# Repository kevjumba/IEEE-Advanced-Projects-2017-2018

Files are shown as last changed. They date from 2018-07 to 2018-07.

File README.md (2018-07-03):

# IEEE-Advanced-Projects-2017-2018

This is the collective work done by myself, Will Fehrnstrom, Ryan Nemiroff, and Amit Golan as part of the Advanced Projects project groups
at UCLA IEEE. 

The objective was the build a fully functioning quadcopter which entails designing the PCB using Eagle Cad and coding much of the
wireless connections and motor control using a MPU6050 and microprocessors(arduino).

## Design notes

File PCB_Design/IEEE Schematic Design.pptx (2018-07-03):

## IEEE Schematic Design

Will Fehrnstrom, Ryan Nemiroff, Kevin Zhang, Amit Golan

## RESET/FTDI

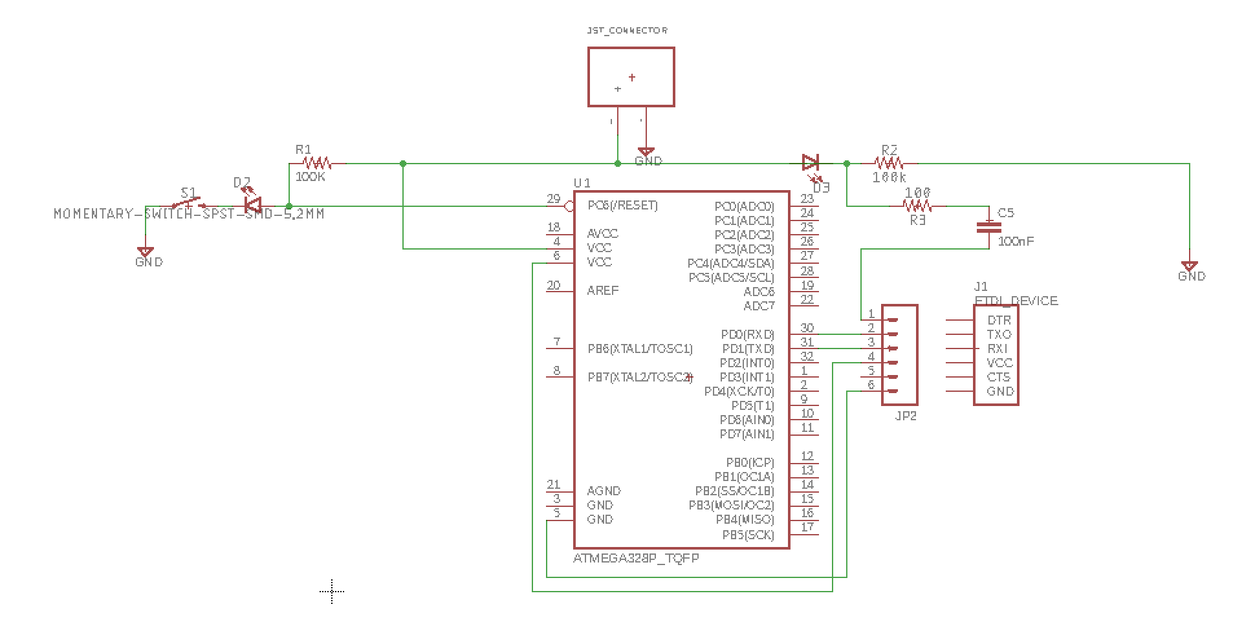
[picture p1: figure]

## Decoupling MCU

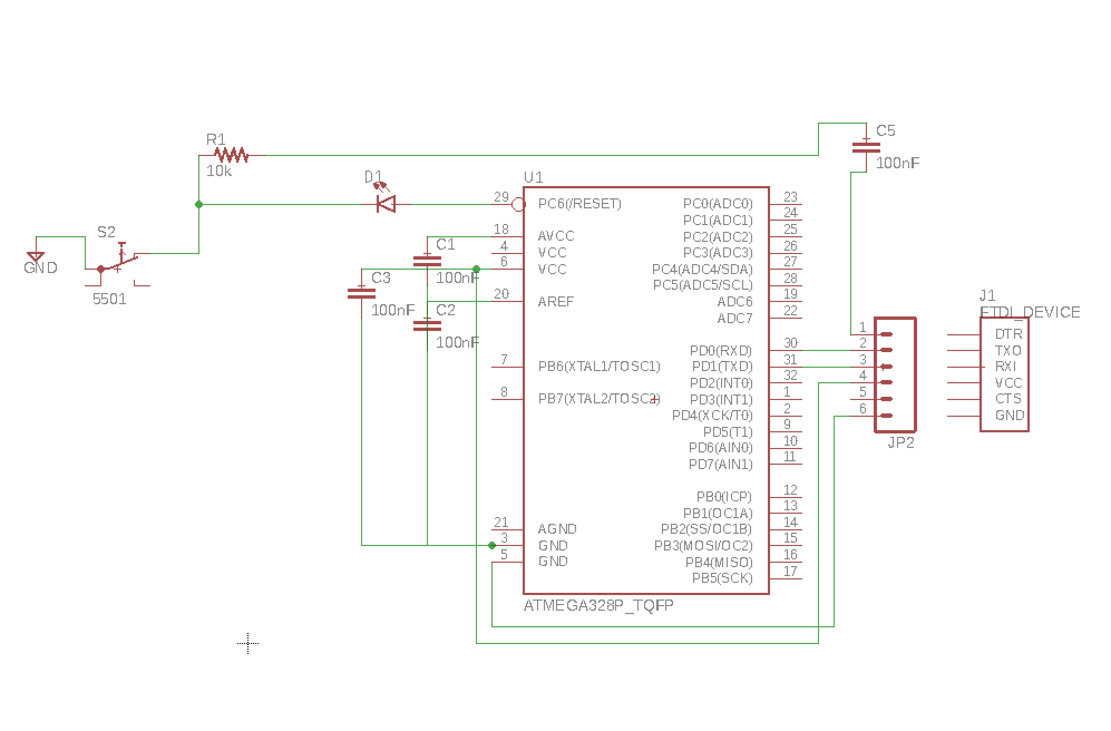
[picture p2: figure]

## Motor Driver

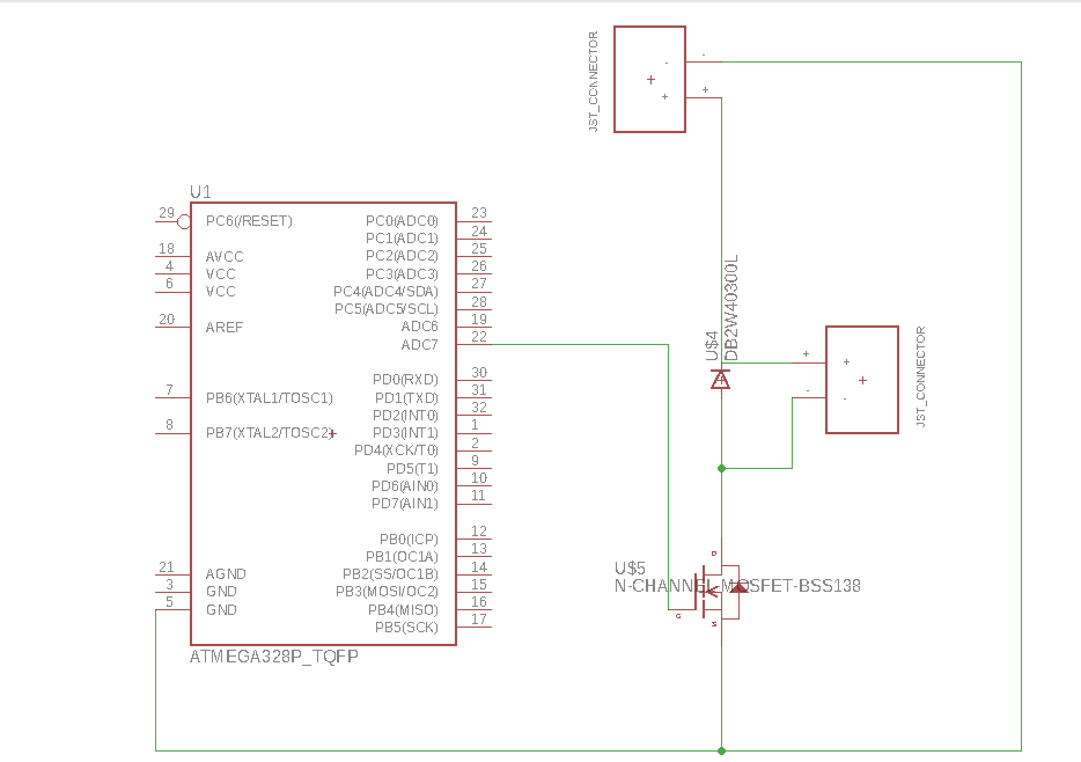
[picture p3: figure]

## IMU to MCU and voltage divider

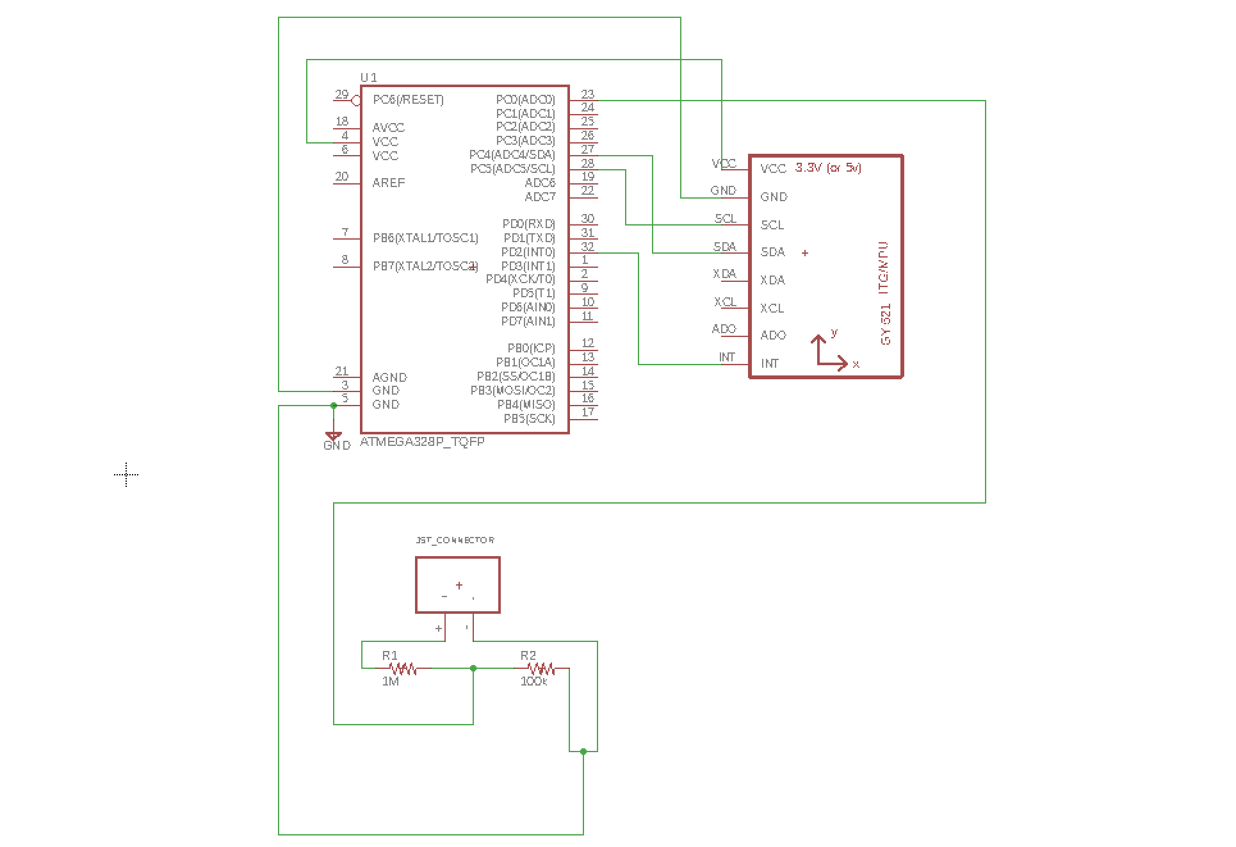
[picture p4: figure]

## RF24 to MCU and buck boost converter

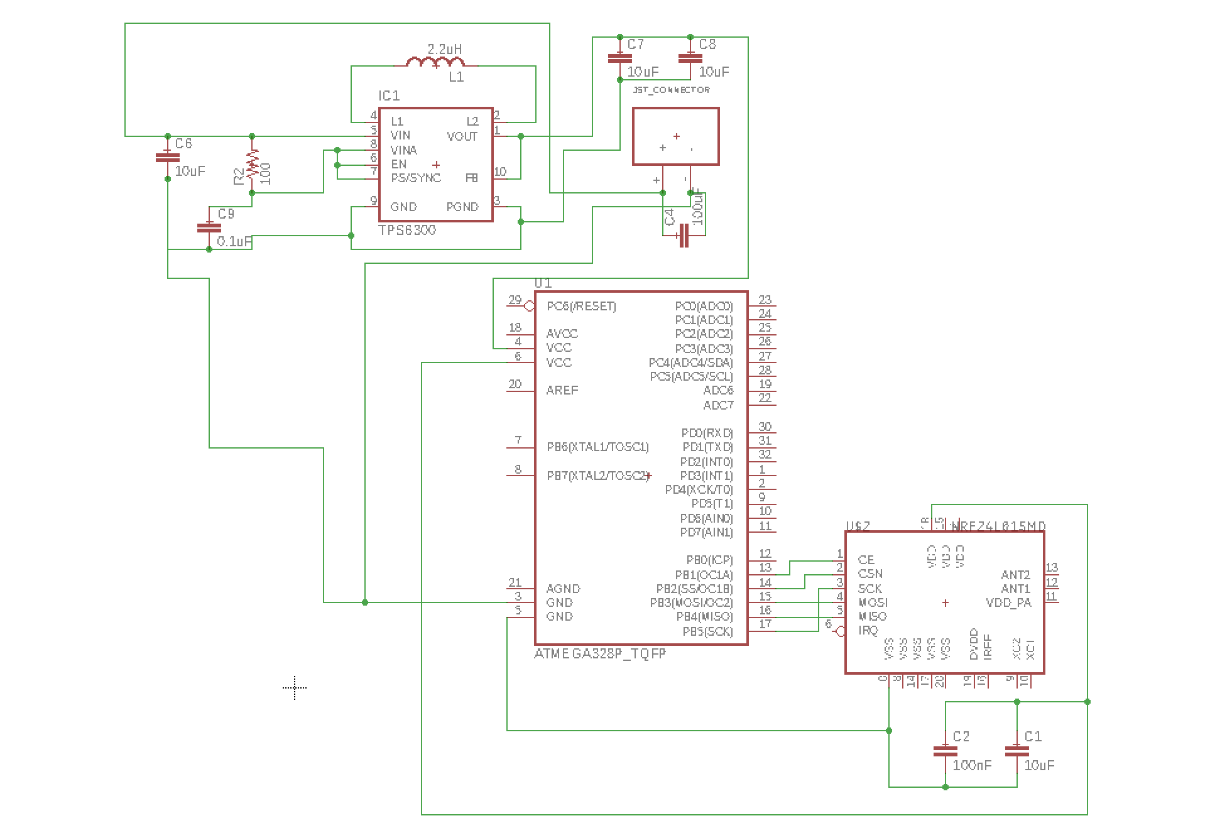
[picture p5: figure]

## Bill of Materials

https://docs.google.com/spreadsheets/d/1XHGL43idXW7UUi7sieGBfkb_WzO-GkUvsEv8cnh8tEY/edit#gid=0

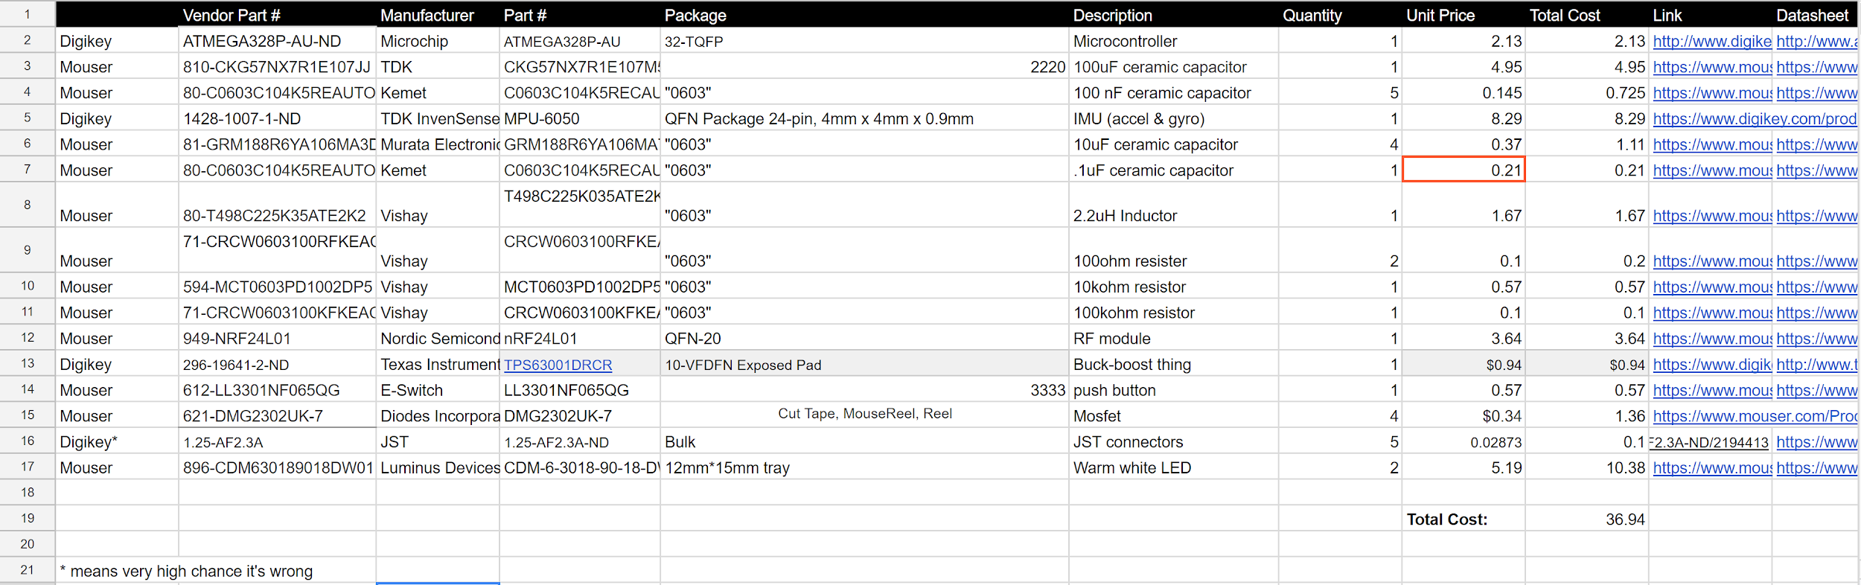
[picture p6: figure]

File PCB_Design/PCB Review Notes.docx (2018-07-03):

- Why is your 100uF cap labeled as 1uF?
- Vcc plane is heavily constricted, especially around your IMU and radio
- Your ground plane is also heavily constricted
- Your oscillator is too far away from your MCU, and the traces are not well laid out. Follow this guideline: link (https://electronics.stackexchange.com/questions/39136/competing-pcb-crystal-layout-recommendations)

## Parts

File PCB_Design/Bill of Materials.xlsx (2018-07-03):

 | Vendor Part # | Manufacturer | Part # | Package | Description | Quantity | Unit Price | Total Cost | Link | Datasheet
Digikey | ATMEGA328P-AU-ND | Microchip | ATMEGA328P-AU | 32-TQFP | Microcontroller | 1 | 2.13 | 2.13 | http://www.digikey.com/product-detail/en/microchip-technology/ATMEGA328P-AU/ATMEGA328P-AU-ND/1832260 | http://ww1.microchip.com/downloads/en/DeviceDoc/Atmel-42735-8-bit-AVR-Microcontroller-ATmega328-328P_Datasheet.pdf
Mouser | 963-JMK316AC6476ML-T | Taiyo Yuden | JMK316AC6476ML-T | 1206 | 100uF ceramic capacitor | 1 | 0.56 | 0.56 | https://www.mouser.com/ProductDetail/Taiyo-Yuden/JMK316AC6476ML-T | https://www.mouser.com/ds/2/396/mlcc11_hq_e-541564.pdf
Mouser | 80-C0603C104K5REAUTO | Kemet | C0603C104K5RECAUTO | "0603" | 100 nF ceramic capacitor | 6 | 0.145 | 0.87 | https://www.mouser.com/ProductDetail/KEMET/C0603C104K5RECAUTO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 | https://www.mouser.com/ds/2/212/KEM_C1090_X7R_ESD-1103328.pdf
 |  |  |  |  |  |  |  | 0
Mouser | 81-GRM188R6YA106MA3D | Murata Electronics | 700B102KW50XT | "0603" | 10uF ceramic capacitor | 1 | 0.37 | 0.37 | https://www.mouser.com/ProductDetail/Murata-Electronics/GRM188R6YA106MA73D | https://www.mouser.com/ds/2/281/GRM188R6YA106MA73-01-1064796.pdf
 |  |  |  |  |  |  |  | 0
 |  |  |  |  |  |  |  | 0
 |  |  |  |  |  |  |  | 0
Mouser | 594-MCT0603PD1002DP5 | Vishay | MCT0603PD1002DP500 | "0603" | 10kohm resistor | 7 | 0.57 | 3.99 | https://www.mouser.com/ProductDetail/Vishay-BC-Components/MCT0603PD1002DP500 | https://www.mouser.com/ds/2/427/mcxhp-1147618.pdf
 |  |  |  |  |  |  |  | 0
 |  |  |  |  |  |  |  | 0
Digikey | RHM220DCT-ND | Rohm Semiconductor | ESR03EZPJ221 | Cut Tape (CT) | 220 ohm resistor | 1 | 0.1 | 0.1 | https://www.digikey.com/product-detail/en/rohm-semiconductor/ESR03EZPJ221/RHM220DCT-ND/1983788 | http://www.rohm.com/web/global/datasheet/ESR01MZPF/esr-e
Mouser | 612-LL3301NF065QG | E-Switch | LL3301NF065QG | 3333 | push button | 1 | 0.57 | 0.57 | https://www.mouser.com/ProductDetail/E-Switch/LL3301NF065QG | https://www.mouser.com/ds/2/140/P090002-267756.pdf
Digikey | 785-1009-2-ND | Alpha & Omega Semiconductor Inc. | AO3414 | Cut Tape | MOSFET | 4 | $0.08 | $0.31 | https://www.digikey.com/product-detail/en/alpha-omega-semiconductor-inc/AO3414/785-1009-2-ND/1855781 | http://aosmd.com/res/data_sheets/AO3414.pdf
Digikey* | 1.25-AF2.3A | JST | 1.25-AF2.3A-ND | Bulk | JST connectors | 5 | 0.02873 | 0.14365 | https://www.digikey.com/product-detail/en/jst-sales-america-inc/1.25-AF2.3A/1.25-AF2.3A-ND/2194413 | https://www.digikey.com/product-detail/en/jst-sales-america-inc/1.25-AF2.3A/1.25-AF2.3A-ND/2194413
Mouser | 581-MM031A220JCT2A | AVX | MM031A220JCT2A | "0603" | 22pF ceramic capacitor | 2 | 0.76 | 1.52 | https://www.mouser.com/ProductDetail/AVX/MM031A220JCT2A | https://www.mouser.com/ds/2/40/AVX-MM-1021715.pdf
Digikey | 160-1446-1-ND | Lite-On Inc. | LTST-C191KGKT | Cut Tape (CT), "0603" | Green indicator LED | 1 | 0.0404 | 0.0404 | https://www.digikey.com/product-detail/en/lite-on-inc/LTST-C191KGKT/160-1446-2-ND/386835 | https://www.digikey.com/en/datasheets/liteoninc/liteon-incltstc191kgkt
Mouser | 667-DB2W40300L | Panasonic | DB2W40300L | 2.6mm x 1.6mm | Schottkey Barrier Diode | 4 | 0.43 | 1.72 | https://www.mouser.com/ProductDetail/Panasonic/DB2W40300L?qs=ZLoPbQp0lqx30DYaaT0Zjg%3D%3D | https://www.mouser.com/ds/2/315/DB2W40300L_E-1141713.pdf
 |  |  |  |  |  |  |  | 0
Mouser |  |  |  |  |  |  |  | 0
NEW: |  |  |  |  |  |  |  | 0
Digikey | 490-1219-2-ND | Murata Electronics | CSTCE8M00G55Z-R0 | Tape & Reel (TR) | 8Mhz Ceramic Resonator | 1 | 0.23 | 0.23 | https://www.digikey.com/product-detail/en/murata-electronics-north-america/CSTCE8M00G55Z-R0/490-1219-2-ND/584427 | https://www.murata.com/~/media/webrenewal/support/library/catalog/products/timingdevice/ceralock/p16e.ashx
Digikey |  |  |  |  |  |  |  | 0
Mouser | 700-MAX1595EUA33 | Maxim Integrated | MAX1595EUA33+ | USOP-8 | Step up/down Charge Pump Regulator | 1 | 4.05 | 4.05 | https://www.mouser.com/ProductDetail/Maxim-Integrated/MAX1595EUA33%2b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 | https://www.mouser.com/ds/2/256/maxim%20integrated%20products_max1595-1178974.pdf
Mouser | 963-LMK107B7105MA-T | Taiyo Yuden | LMK107B7105MA-T | "0603" | 1µF capacitor | 2 | 0.1 | 0.2 | https://www.mouser.com/ProductDetail/Taiyo-Yuden/LMK107B7105MA-T | https://www.mouser.com/ds/2/396/mlcc_all_e-1149778.pdf
Mouser | 963-LMK107B7224MA-T | Taiyo Yuden | LMK107B7224MA-T | "0603" | 0.22uF capacitor | 1 | 0.22 | 0.22 | https://www.mouser.com/ProductDetail/Taiyo-Yuden/LMK107B7224MA-T | https://www.mouser.com/ds/2/396/mlcc_all_e-1149778.pdf
 |  |  |  |  |  |  | Total Cost: | 17.02205
Archived Components | NOT IN USE
Mouser | 896-CDM630189018DW01 | Luminus Devices | CDM-6-3018-90-18-DW01 | 12mm*15mm tray | Warm white LED | 2 | 5.19 | 10.38 | https://www.mouser.com/productdetail/luminus-devices/cdm-6-3018-90-18-dw01 | https://www.mouser.com/ds/2/245/Luminus%20Devices-7-27-2017-CDM_Prelim-1177391.pdf
 | 535-10212-1-ND | Abracon LLC | ABLS-8.000MHZ-B4-T | HC49/US | 8MHz crystal | 1 | 0.25 | 0.25 | https://www.digikey.com/product-detail/en/abracon-llc/ABLS-8.000MHZ-B4-T/535-10212-1-ND/2184247 | http://www.abracon.com/Resonators/abls.pdf
Mouser | 80-T498C225K35ATE2K2 | Vishay | T498C225K035ATE2K2 | "0603" | 2.2uH Inductor (no it's not) | 1 | 1.67 | 1.67 | https://www.mouser.com/ProductDetail/KEMET/T498C225K035ATE2K2 | https://www.mouser.com/ds/2/212/KEM_T2053_T498_AUTO-1093583.pdf
Mouser | 449-LFXTAL019715REEL | IQD | LFXTAL019715Reel | 11.4 mm x 4.9mm | 19 MHz Crystal Oscillator | 1 | 0.21 | 0.21 | https://www.mouser.com/ProductDetail/IQD/LFXTAL019715Reel | https://www.mouser.com/ds/2/741/LFXTAL019715Reel-992778.pdf
Digikey | 296-42650-1-ND | Texas Instruments | TPS63051RMWR | VQFN 2.5mm x 2.5mm | Buck-boost converter | 1 | $0.94 | $0.94 | https://www.digikey.com/product-detail/en/texas-instruments/TPS63051RMWR/296-42650-1-ND/5455915 | http://www.ti.com/lit/ds/symlink/tps63050.pdf
Mouser | 81-LQM18PN1R5MFHD | Murata Electronics | LQM18PN1R5MFHD | "0603" | 1.5uH inductor | 1 | 0.45 | 0.45 | https://www.mouser.com/ProductDetail/Murata-Electronics/LQM18PN1R5MFHD | https://www.mouser.com/ds/2/281/JELF243B-0043-1102176.pdf
Mouser | 963-TMK063CG102JT-F | Taiyo-Yuden | TMK063CG102JT-F | "0603" | 1nF ceramic capacitor | 1 | 0.1 | 0.1 | https://www.mouser.com/ProductDetail/Taiyo-Yuden/TMK063CG102JT-F | https://www.mouser.com/ds/2/396/mlcc01_e-3194.pdf
Mouser | 667-ERJ-1GNJ105C | Panasonic | ERJ-1GNJ105C | "0603" | 1Mohm resistor | 1 | 0.21 | 0.21 | https://www.mouser.com/ProductDetail/Panasonic/ERJ-1GNJ105C?qs=sGAEpiMZZMu61qfTUdNhG1IKPAnaLGejICRtqOthr3w%3d | https://industrial.panasonic.com/ww/products/resistors/chip-resistors/general-purpose-chip-resistors/thick-film-chip-resistors/ERJ1GNJ120C
71-CRCW0603100RFKEAC | Vishay | CRCW0603100RFKEAC | "0603" | 100ohm resister | 1 | 0.1 | 0.1 | https://www.mouser.com/ProductDetail/Vishay/CRCW0603100RFKEAC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 | https://www.mouser.com/ds/2/427/crcwce3-1223726.pdf

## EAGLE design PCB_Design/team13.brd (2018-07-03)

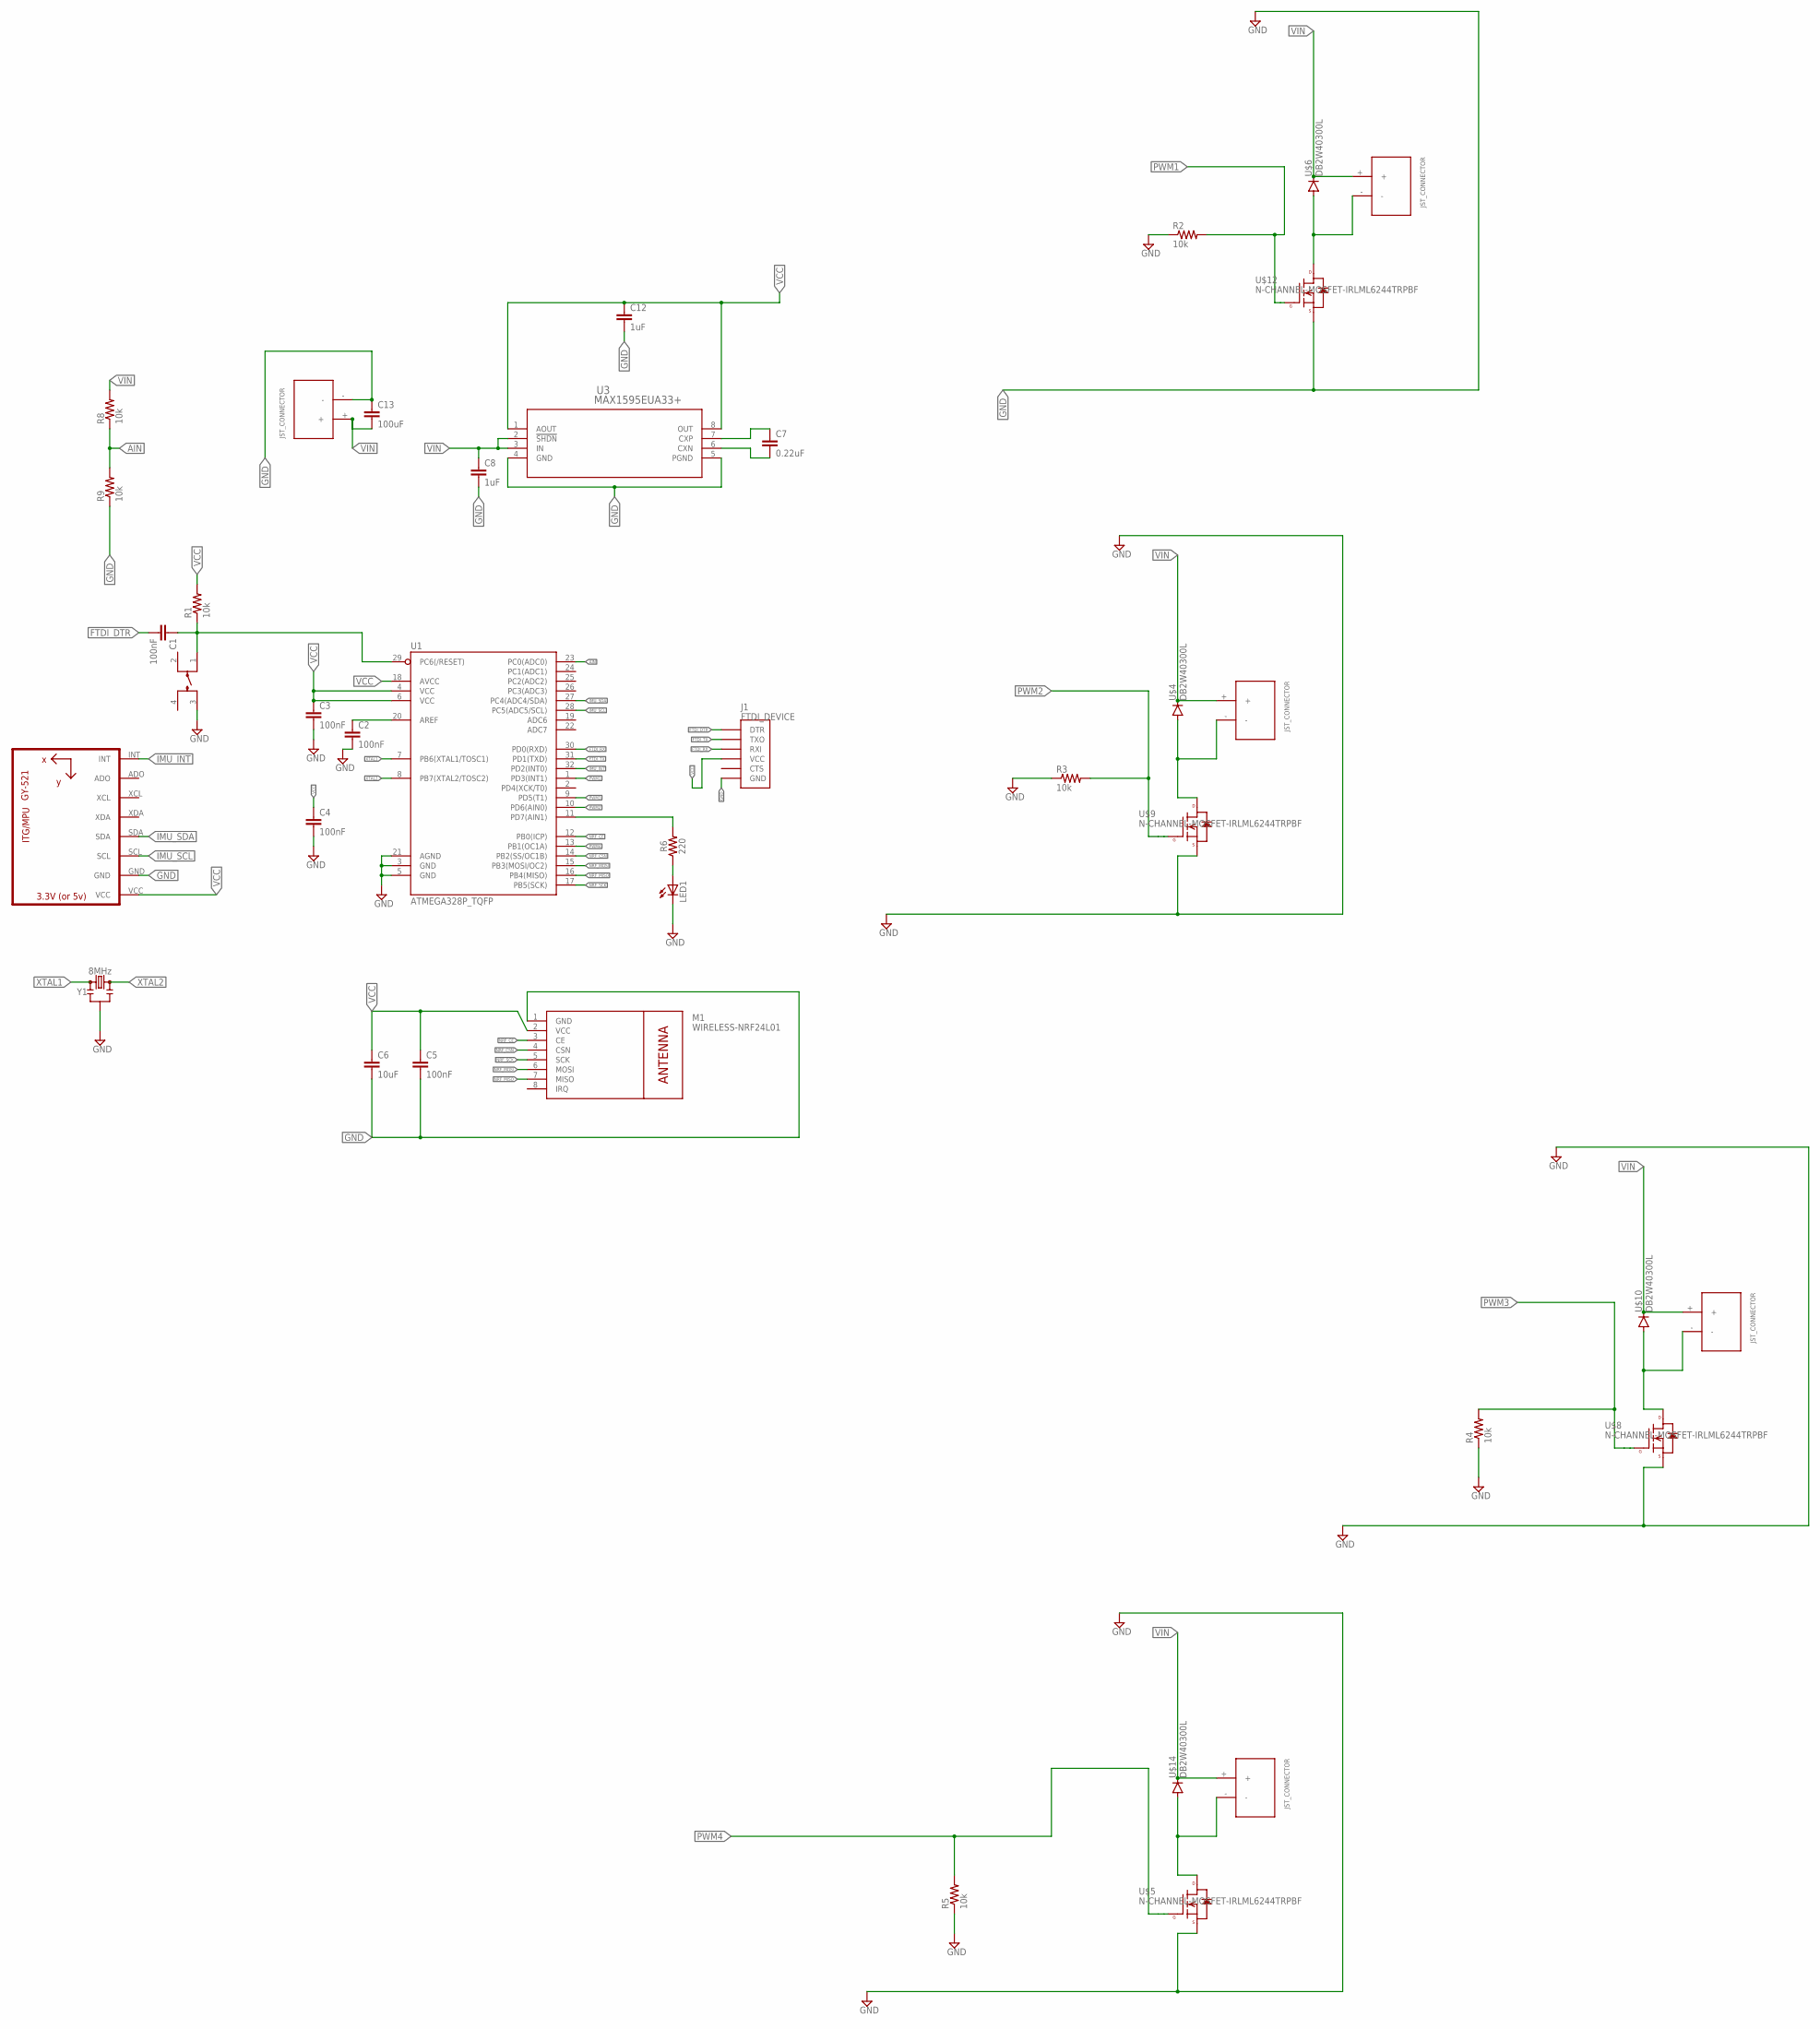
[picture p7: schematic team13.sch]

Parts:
C1, C2, C3, C4, C5: 100nF; C0603
C6: 10uF; C0603
C7: 0.22uF; C0603
C8, C12: 1uF; C0603
C13: 100uF; C1206
J1: FTDI_DEVICE; FTDI_DEVICE_SIDE
LED1: LED1206; LED-1206
M1: WIRELESS-NRF24L01
R1, R8, R9: 10k; R0603
R2, R3, R4, R5: 10k; 0603-RES
R6: 220; 0603
U1: ATMEGA328P_TQFP; TQFP32-08
U2: GY-521MPU6050; GY-521
U3: MAX1595EUA33+; 21-0036K
U$1: LL3301NF065QG
U$3, U$7, U$11, U$15, U$19: JST_CONNECTOR_FEMALE
U$4, U$6, U$10, U$14: DB2W40300L; MINI2-F3-B
U$5, U$8, U$9, U$12: N-CHANNEL-MOSFET-IRLML6244TRPBF; SOT23-3
Y1: 8MHz; RESONATOR-SMD-3.2X1.3

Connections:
AIN: R8.1, R9.2, U1.23 (PC0(ADC0))
FTDI_DTR: C1.2, J1.P$1 (DTR)
FTDI_RX: J1.P$3 (RXI), U1.30 (PD0(RXD))
FTDI_TX: J1.P$2 (TXO), U1.31 (PD1(TXD))
GND: C2.2, C3.2, C4.2, C5.2, C6.2, C8.2, C12.2, C13.1, J1.P$6 (GND), LED1.C, M1.1 (GND), R2.1, R3.1, R4.1, R5.1, R9.1, U1.3 (GND), U1.5 (GND), U1.21 (AGND), U2.GND, U3.4 (GND), U3.5 (PGND), U$1.3, U$5.2 (S), U$8.2 (S), U$9.2 (S), U$12.2 (S), U$19.-, Y1.2
IMU_INT: U1.32 (PD2(INT0)), U2.INT
IMU_SCL: U1.28 (PC5(ADC5/SCL)), U2.SCL
IMU_SDA: U1.27 (PC4(ADC4/SDA)), U2.SDA
unnamed: C1.1, R1.1, U1.29 (PC6(/RESET)), U$1.1
unnamed: C2.1, U1.20 (AREF)
unnamed: U$3.-, U$4.POS (PPIN), U$9.3 (D)
unnamed: C7.1, U3.7 (CXP)
unnamed: R6.2, U1.11 (PD7(AIN1))
unnamed: U$6.POS (PPIN), U$7.-, U$12.3 (D)
unnamed: C7.2, U3.6 (CXN)
unnamed: LED1.A, R6.1
unnamed: U$8.3 (D), U$10.POS (PPIN), U$11.-
unnamed: U$5.3 (D), U$14.POS (PPIN), U$15.-
NRF_CE: M1.3 (CE), U1.12 (PB0(ICP))
NRF_CSN: M1.4 (CSN), U1.14 (PB2(SS/OC1B))
NRF_MISO: M1.7 (MISO), U1.16 (PB4(MISO))
NRF_MOSI: M1.6 (MOSI), U1.15 (PB3(MOSI/OC2))
NRF_SCK: M1.5 (SCK), U1.17 (PB5(SCK))
PWM1: R2.2, U1.1 (PD3(INT1)), U$12.1 (G)
PWM2: R3.2, U1.10 (PD6(AIN0)), U$9.1 (G)
PWM3: R4.2, U1.9 (PD5(T1)), U$8.1 (G)
PWM4: R5.2, U1.13 (PB1(OC1A)), U$5.1 (G)
VCC: C3.1, C4.1, C5.1, C6.1, C12.1, J1.P$4 (VCC), M1.2 (VCC), R1.2, U1.4 (VCC), U1.6 (VCC), U1.18 (AVCC), U2.VCC, U3.1 (AOUT), U3.8 (OUT)
VIN: C8.1, C13.2, R8.2, U3.2 (!SHDN), U3.3 (IN), U$3.+, U$4.NEG (GPIN), U$6.NEG (GPIN), U$7.+, U$10.NEG (GPIN), U$11.+, U$14.NEG (GPIN), U$15.+, U$19.+
XTAL1: U1.7 (PB6(XTAL1/TOSC1)), Y1.1
XTAL2: U1.8 (PB7(XTAL2/TOSC2)), Y1.3

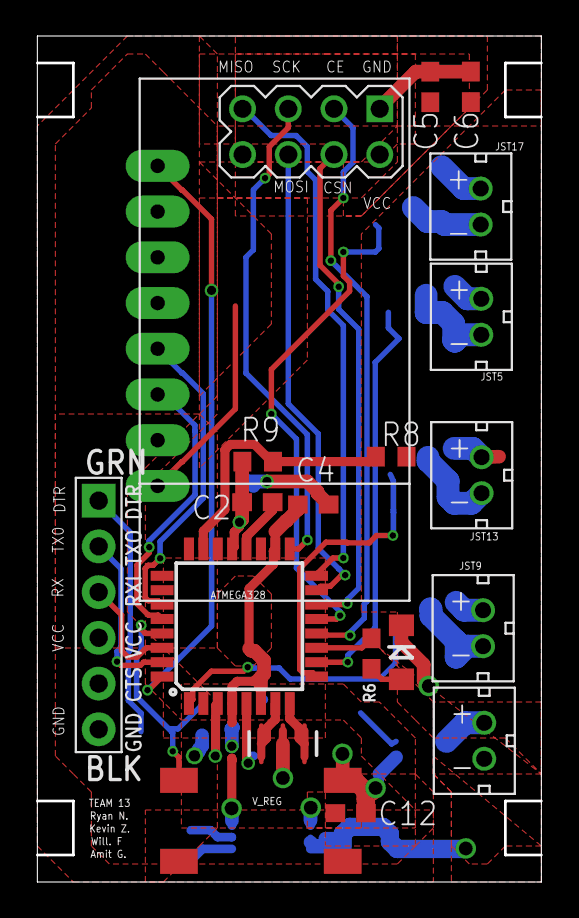
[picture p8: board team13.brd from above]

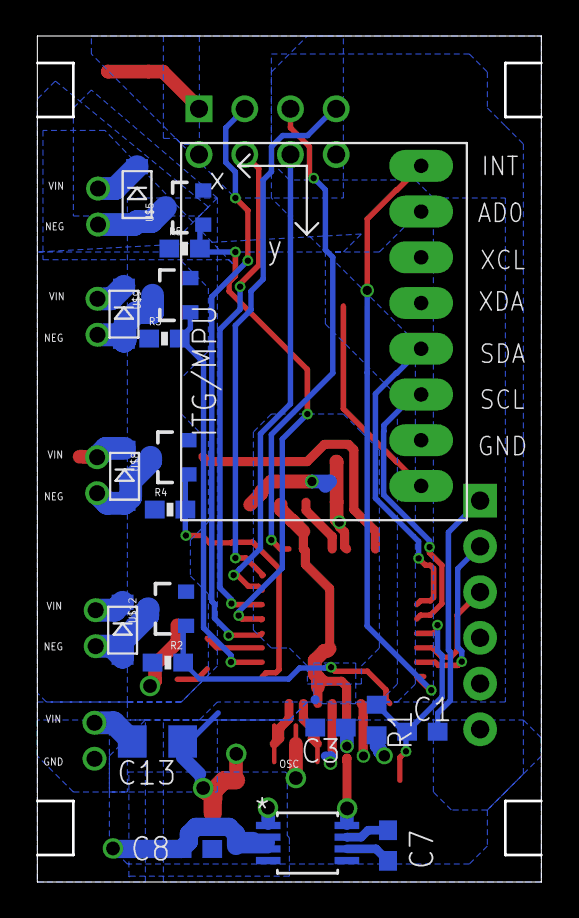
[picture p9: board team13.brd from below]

Board: 2 copper layers, 28.0 x 47.0 mm, 39 parts (20 on the bottom side), 31 nets.

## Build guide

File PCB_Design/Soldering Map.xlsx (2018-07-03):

Order To Solder | Component | PCB Val | Side
1 | RHM220DCT-ND (220 Ohm Resistor) Cut Tape | R6 | top | done
2 | LTST-C191KGKT, "0603" | GREEN LED, DIODE Next to R6 | top
3 | 10K Ohm (594-MCT0603PD1002DP5) | R9 | top | done
4 | 10K Ohm (594-MCT0603PD1002DP5) | R8 | top | done
5 | 100 nf Capacitor (C0603C104K5RECAUTO) | C2 | top | done
6 | 100 nf Capacitor (C0603C104K5RECAUTO) | C4 | top | done
7 | 100 nF Capacitor | C5 | top | done
8 | 10 uF Capacitor | C6 | top | done
9 | 8MHz Resonator (CSTCE8M00G55Z-R0) |  | top
10 | 1 uF Capacitor | C12 | top | done
11 | C13 |  | bottom | done
 | C8 |  | bottom | done
 | C7 |  | bottom | done

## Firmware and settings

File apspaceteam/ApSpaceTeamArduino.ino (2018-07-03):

#include <nRF24L01.h>
//#include <printf.h>
#include <RF24.h>
#include <RF24_config.h>

#define CE_PIN 9
#define CSN_PIN 10
#define READING_PIPE 0xC2C2C2C2C2
#define WRITING_PIPE 0xE7E7E7E7E7
#define PAYLOAD_SIZE 32

#define BTN_1_PIN 6
#define BTN_2_PIN 7
#define BTN_3_PIN 8

#define LED_1 0x01
#define LED_2 0x02
#define LED_3 0x03

#define CORRECT_BUTTONS 0x04
#define WRONG_BUTTONS 0x05

uint8_t ledSequence[PAYLOAD_SIZE];
uint8_t sequenceIndex = 0;
bool waitForSequence = true;
bool btn1Prev = LOW;
bool btn2Prev = LOW;
bool btn3Prev = LOW;

RF24 rf24(CE_PIN, CSN_PIN);
uint8_t received_data[PAYLOAD_SIZE];

int curr_index = 0;

void setup() {
  Serial.begin(57600);
  pinMode(BTN_1_PIN, INPUT);
  pinMode(BTN_2_PIN, INPUT);
  pinMode(BTN_3_PIN, INPUT);
  rf24.begin();
  rf24.setChannel(13);
  rf24.setPALevel(RF24_PA_MAX);
  rf24.openReadingPipe(1, READING_PIPE);
  rf24.openWritingPipe(WRITING_PIPE);
  rf24.setCRCLength(RF24_CRC_16);
  rf24.setPayloadSize(PAYLOAD_SIZE);

  rf24.startListening();

  Serial.print("starting");
}

void loop() {
  //test(); 
  bool btn1State = digitalRead(BTN_1_PIN);
  bool btn2State = digitalRead(BTN_2_PIN);
  bool btn3State = digitalRead(BTN_3_PIN);
  if (waitForSequence) {
    if(rf24.available()) {
      rf24.read(&ledSequence, PAYLOAD_SIZE);
      Serial.println(ledSequence[curr_index]);
      if (ledSequence[0] != 0) {
        rf24.stopListening();
        waitForSequence = false;
      }
      curr_index++;
    }
  } else {
    if (btn1State == HIGH && btn1Prev == LOW) {
      checkInput(LED_1);
    } else if (btn2State == HIGH && btn2Prev == LOW) {
      checkInput(LED_2);
    } else if (btn3State == HIGH && btn3Prev == LOW) {
      checkInput(LED_3);
    } 
  }
  btn1Prev = btn1State;
  btn2Prev = btn2State;
  btn3Prev = btn3State;
}

void checkInput(uint8_t LED_NUM) {
  if (LED_NUM == ledSequence[sequenceIndex]) {
    sequenceIndex++;
    if (sequenceIndex == PAYLOAD_SIZE || ledSequence[sequenceIndex] == 0) {
      uint8_t message[1] = {CORRECT_BUTTONS};
      Serial.println("RIGHT BUTTONS");
      rf24.write(message, 1);
      sequenceIndex = 0;
      waitForSequence = true;
      rf24.startListening();
    }
  } else {
    uint8_t message[1] = {WRONG_BUTTONS};
    Serial.println("WRONG BUTTONS");
    rf24.write(message, 1);
    sequenceIndex = 0;
    waitForSequence = true;
    rf24.startListening();
  }
}

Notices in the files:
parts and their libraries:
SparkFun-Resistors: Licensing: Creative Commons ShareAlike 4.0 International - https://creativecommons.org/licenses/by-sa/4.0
